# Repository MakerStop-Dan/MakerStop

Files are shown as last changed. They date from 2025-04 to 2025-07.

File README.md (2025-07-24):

# MakerStop
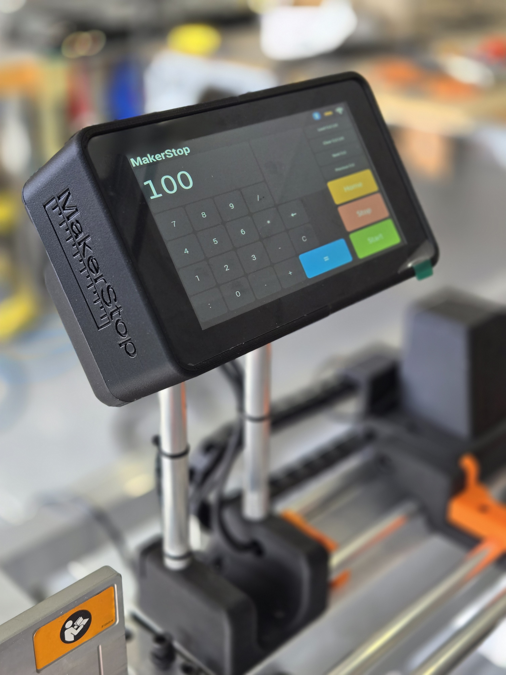
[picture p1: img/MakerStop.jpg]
MakerStop


Kits will be made available to purchase from www.makerstop.com.au

Contact - info@makerstop.com.au

Instagram - instagram.com/makerstop_

https://www.youtube.com/@MakerStop_au

**MakerStop** is an automatic length stop system designed for Mitre saws, band saws and drill presses used by Makers, metal fabricators, carpenters, and weekend warriors who demand precision without paying commercial-level prices.

Born out of necessity, MakerStop was developed in a small home garage where space, efficiency, and accuracy are the difference between thriving and burnout. As a full-time metal fabricator, I built this tool to meet the real-world demands of daily cutting tasks.

My goal is to make automation accessible—without the bloated cost or complexity. MakerStop is modular, lightweight, and affordable, and it challenges some of the typical assumptions in DIY automation and CNC hardware. If you're curious about how and why certain choices were made, check out the **Design Decisions** section below.

## Features
- Repeatable automatic stop positioning
- Mostly 3d Printed
- Easy assembly
- ESP32 Controller
- Raspberry pi zero 2w and custom python software for control
- Cut list functionality
- Customizable in length
- Low BOM cost
- Built for mitre saws, cold saws, drop saws, etc.

## 📄 License

- 🧠 **Software (code/scripts)** — [Mozilla Public License 2.0](https://www.mozilla.org/en-US/MPL/2.0/)
- 🛠️ **Design files (3D models, CAD, documentation)** — [CC BY-NC 4.0](https://creativecommons.org/licenses/by-nc/4.0/)

> Feel free to use, remix, and improve — just give credit.  
> Commercial use of hardware designs is **not allowed** without permission.  
> For licensing inquiries, reach out at info@makerstop.com.au

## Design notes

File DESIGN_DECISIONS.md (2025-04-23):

# MakerStop Design Decisions

The purpose of this page is to communicate my intentions through my design decisions. This includes the aspects of the project I consider most important, and the reasoning behind those priorities. It’s here to give context to current and future contributors, customers, or anyone digging into the project.

## Overview

MakerStop is a modular, 3D-printable automatic length stop system aimed at small fabrication shops, hobbyists, and maker spaces. It’s designed to be low-cost, highly customizable, and easy to assemble or maintain. The project balances printability, mechanical reliability, and accessibility.

**Key goals:**
- Must be adjustable in length to suit different applications
- Have an easy to use touch screen interface
- Cut list functionality 
- Needs to be light weight and compact enough to transport and ship
- Needs to be accurate and reliable

## Linear Motion

Linear motion is central to MakerStop’s function. Here's how I approached it:

- **Belt-Driven System:** I chose a GT3 timing belt as it is affordable, accurate and easy to source. A belt driven system allows for customizable length of motion. 
  
- **Linear Rails** The original prototype used linear rails and bearings as i had them left over from a CNC Build. While this is a great option, linear rails and bearings are expensive, heavy and difficult to source locally. 

I then worked on an MPCNC style carriage that used internally placed 15x5x5 Bearings. Another great option but it made for large complecated prints. 

I then took the Elon approach and began to question weather bearings were even necessary. In short, for this application, they aren't. I opted for 16mm round aluminium tube for the linear rails. The carriage hugs the rails with very little friction and allows for the affordability and modularity set out in the Goals section above. 

- **User Interface** It is tempting to build a mobile application to allow users to bring their own device but the decision was made to keep to the raspberry pi and touch screen interface to keep the user experience consistent and maintain a certain level of simplicity. 

**Firmware** FLUIDNC is a robust cnc firmware for ESP32 base controllers and works perfectly for this application. No need to reinvent the wheel. 

**Controller** Currently prototyping a custom controller design featuring ESP32 module and TB6600 stepper driver on the same board. It will also have a 5v rail to power the raspberry pi zero 2 and touch screen. Combining everything onto a single board will greatly reduce the space required in the touch screen enclosure, simplify the BOM and reduce the over all bom cost and assembly time.

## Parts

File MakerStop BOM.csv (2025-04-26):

 | QTY | Price | Total | Supplier
Raspberry Pi Zero | 1 | $29.45 | $506.12 | https://core-electronics.com.au/raspberry-pi-zero-2-w-wireless.html
Raspberry Pi SD Card 32gb | 1 | $17.20 |  | https://core-electronics.com.au/raspberry-pi-a2-class-sd-card-32gb.html
Raspberry Pi Touch Screen - WaveShare Disp -7a | 1 | $91.95 |  | https://core-electronics.com.au/7-touch-display-kit-for-raspberry-pi-zero-1024600-pixel-touch-screen.html
Limit Switch - Mechanical Key - Cherry MX | 1 | $2.45 |  | https://core-electronics.com.au/cherry-mx-switch.html
Nema 23 Stepper Motor high torque | 1 | $52.45 |  | https://www.makerstore.com.au/product/elec-nema23-635-ht
Stepper Driver - Pibot rev 2.3 | 1 | $22.00 |  | https://www.makerstore.com.au/product/pidrb230b01/
GT3 Timing Belt - 3m | 3 | $28.20 |  | https://www.makerstore.com.au/product/belt-gt3-1m/?pewc_key=503a48157eb3d2cdd4758ead74c50f1c
GT3 Pulley | 1 | $12.55 |  | https://www.makerstore.com.au/product/belt-gt3-10mm-635/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
Cable Chain 10x10 | 2 | $26.26 |  | https://www.makerstore.com.au/product/hard-dragchain-1010
Bearings 16x5x5 | 4 | $9.20 |  | https://www.makerstore.com.au/product/bear-6252rs/
Shielded Cable 6mm 4 core shielded | 4 | $17.64 |  | https://www.makerstore.com.au/product/elec-cable-4s-705
M5 x 10mm Cap Head Screws - Black - Pack of 10 | 1 | $1.26 |  | https://www.makerstore.com.au/product/bolt-m5-cap
M5 x 25mm Cap Head Screws - Black - Pack of 10 | 2 | $4.70 |  | https://www.makerstore.com.au/product/bolt-m5-cap
M8 x 20mm Cap Head Screws - Black - Pack of 10 | 1 | $4.20 |  | https://www.makerstore.com.au/product/bolts-m8-cap
Filament Pla CF 1kg - Black | 1 | $48.99 |  | https://au.store.bambulab.com/products/pla-cf
Filament PLA Matte - 1kg - Orange | 1 | $30.99 |  | https://au.store.bambulab.com/products/pla-matte?id=42647402381475
Power Supply 24v 7.5 amp adapter | 1 | $89.95 |  | https://www.auselectronicsdirect.com.au/24v-dc-7.5a-desktop-power-adapter-with-2.5mm-dc-pl
16mm Round Tube - Aluminium | 2 | $16.68

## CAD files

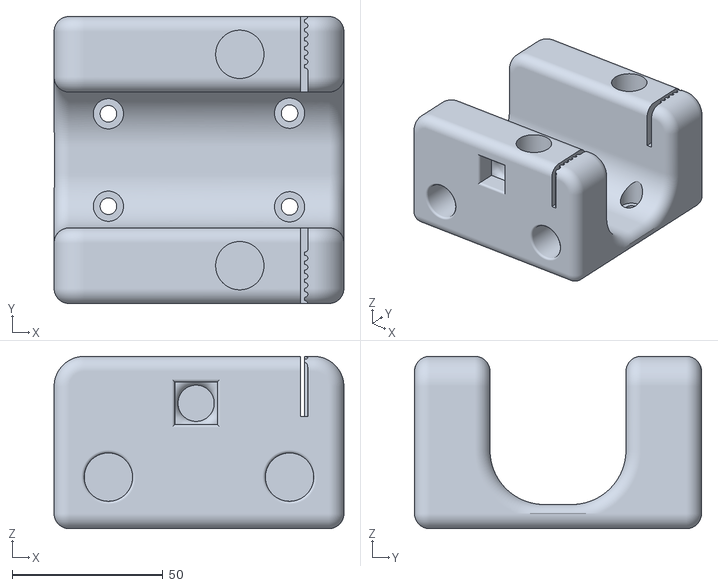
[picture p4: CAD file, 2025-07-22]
STL's/MakerStop - Home Base.stl
96.0 x 95.1 x 57.1

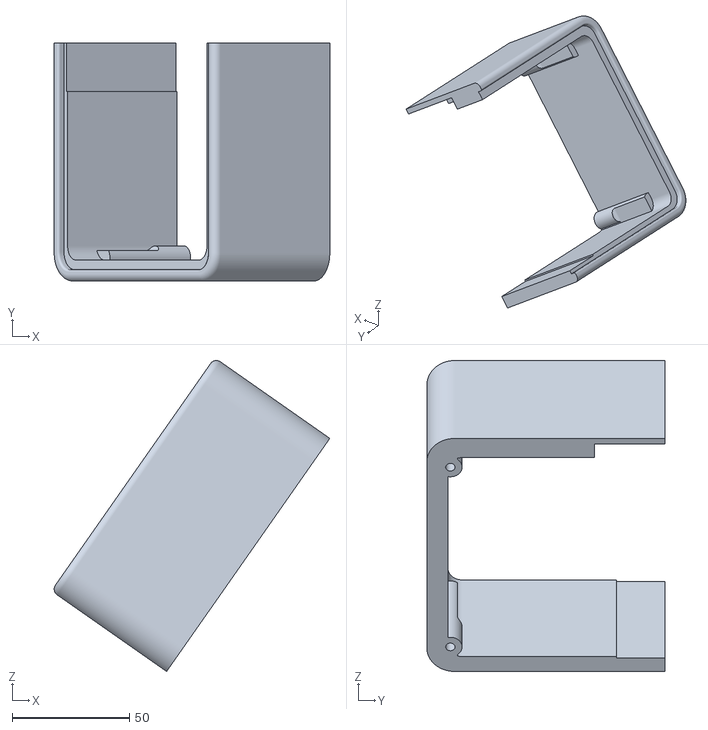
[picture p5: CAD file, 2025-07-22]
STL's/MakerStop - Console Right.stl
117.6 x 101.6 x 132.7

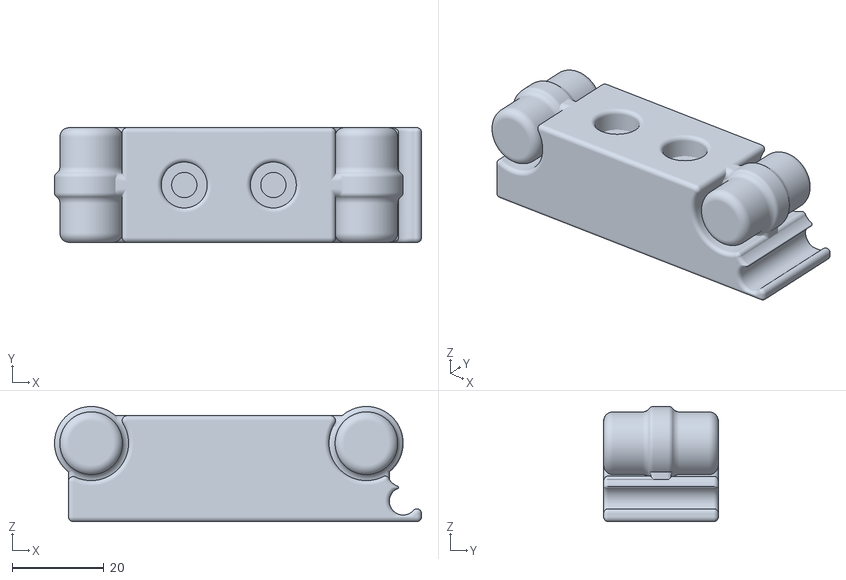
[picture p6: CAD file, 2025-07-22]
STL's/MakerStop - Rail Joiner .stl
80.0 x 25.0 x 25.1

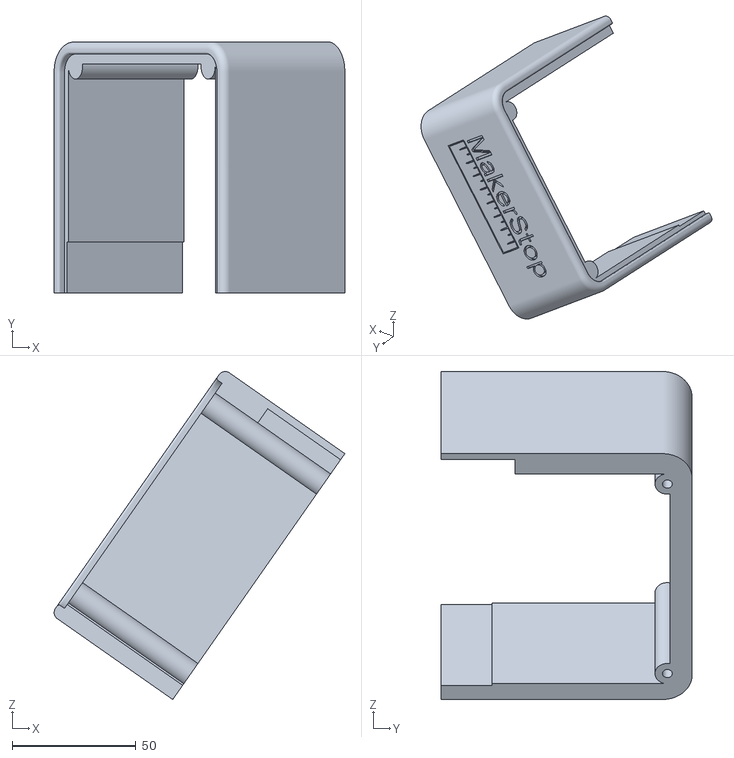
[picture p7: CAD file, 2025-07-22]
STL's/MakerStop - Console Left.stl
117.6 x 101.6 x 132.7

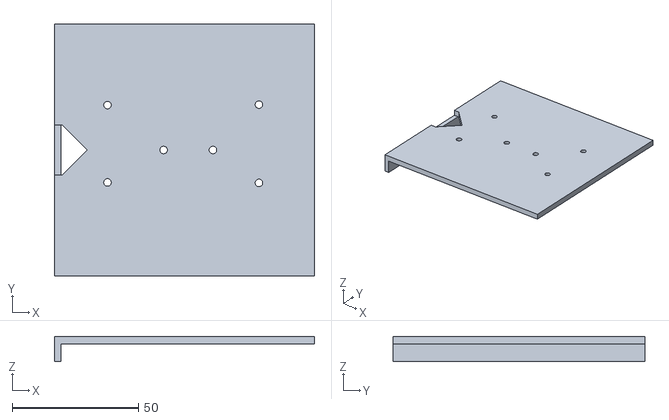
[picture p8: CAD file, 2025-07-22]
STL's/Marking jig.stl
103.0 x 100.0 x 10.0

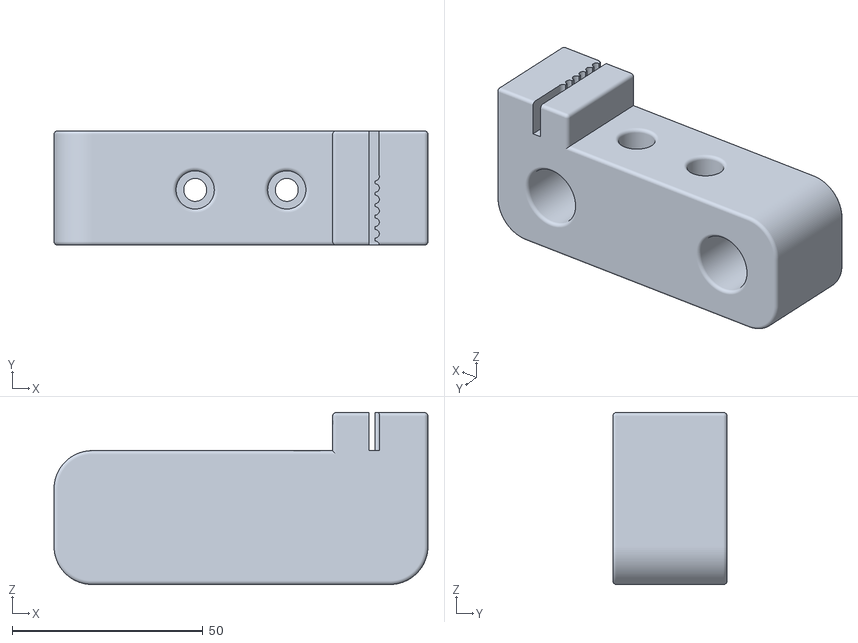
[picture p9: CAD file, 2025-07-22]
STL's/MakerStop - Rail End Mount.stl
98.0 x 30.0 x 45.1

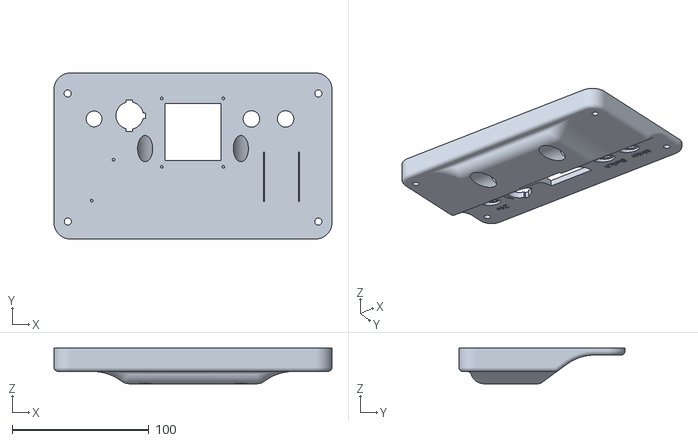
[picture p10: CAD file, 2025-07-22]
STL's/MakerStop - Console Back .stl
203.2 x 121.4 x 26.0

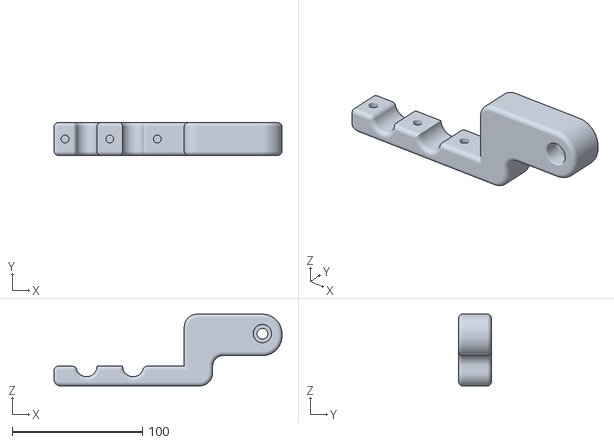
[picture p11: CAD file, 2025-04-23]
STL's/MakerStop - Carriage Arm Bottom Right.stl
175.0 x 25.0 x 55.1

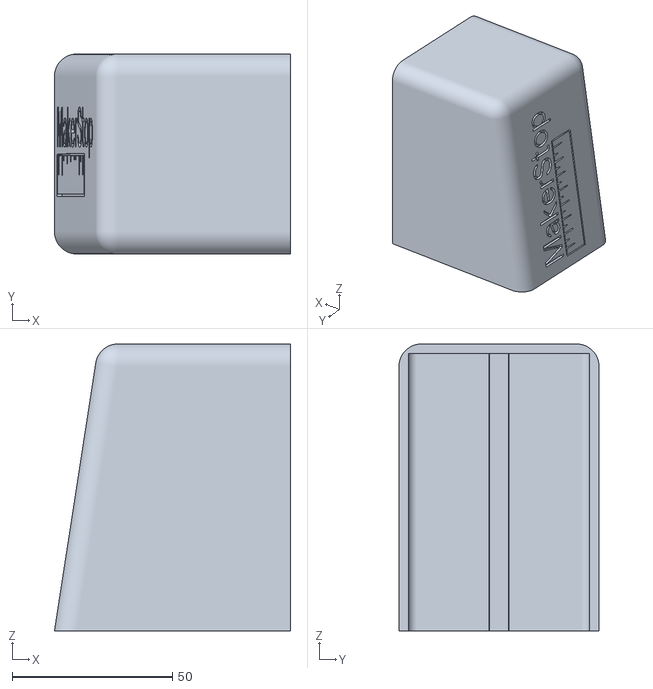
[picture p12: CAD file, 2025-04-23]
STL's/MakerStop - Motor Cover.stl
73.6 x 62.4 x 89.5

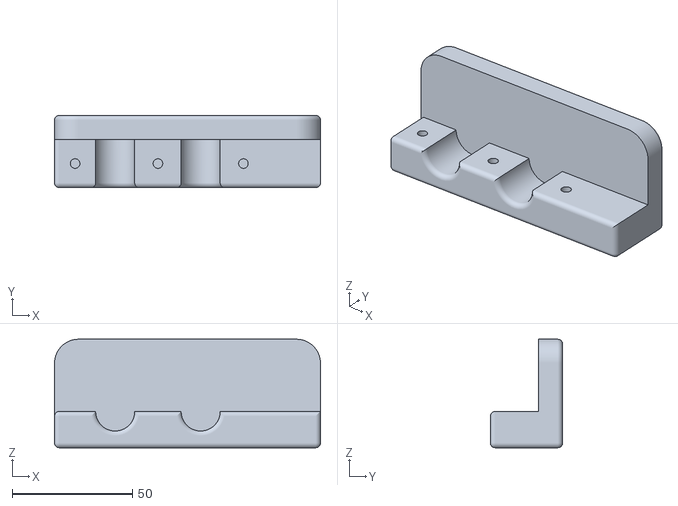
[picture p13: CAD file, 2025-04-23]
STL's/MakerStop - Stop Block.stl
110.5 x 30.0 x 45.1

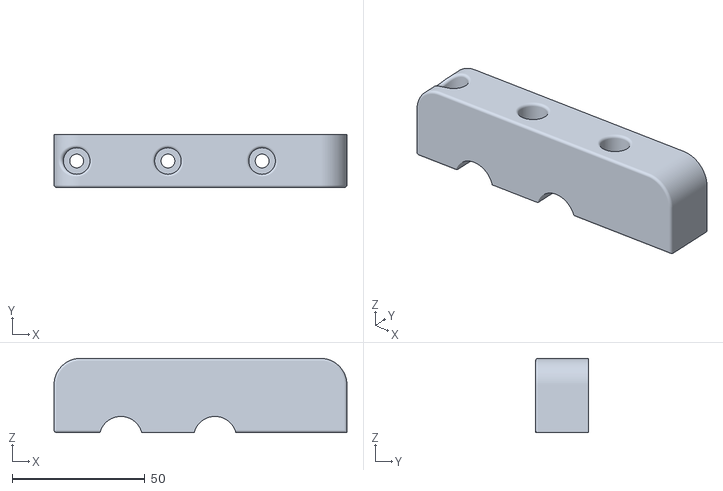
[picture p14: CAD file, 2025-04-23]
STL's/MakerStop - Stop Clamp.stl
110.5 x 20.0 x 28.0

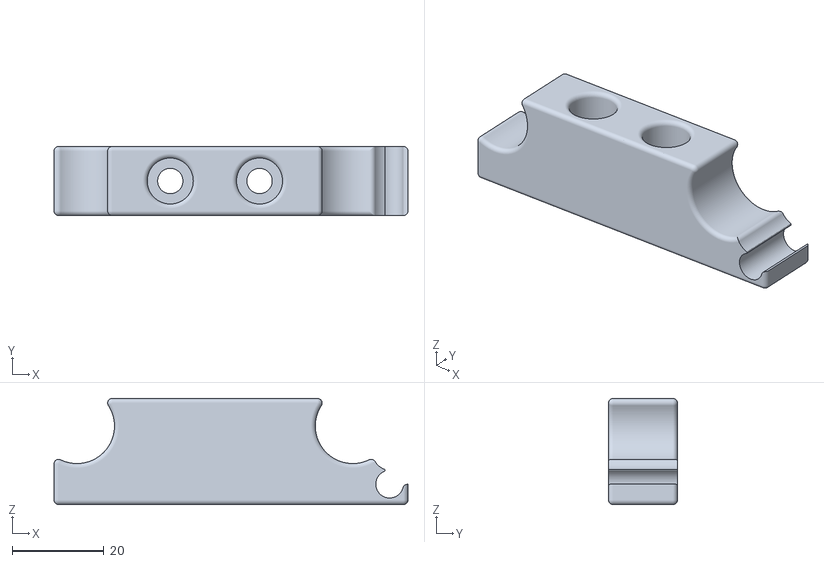
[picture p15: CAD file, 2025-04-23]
STL's/MakerStop - Rail Support.stl
77.0 x 15.0 x 23.1

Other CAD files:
STL's/MakerStop - Carriage Arm Bottom Left.stl

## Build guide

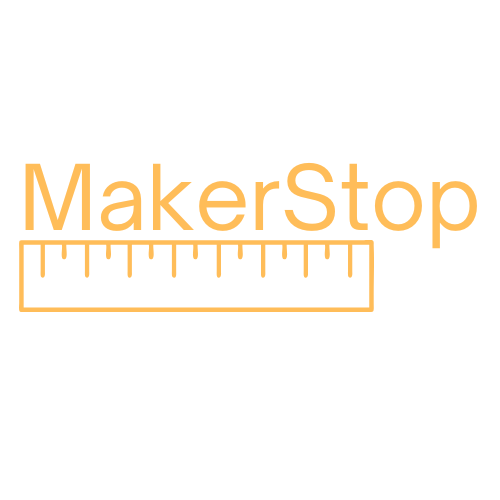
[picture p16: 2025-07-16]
Code/assets/MakerStop.png

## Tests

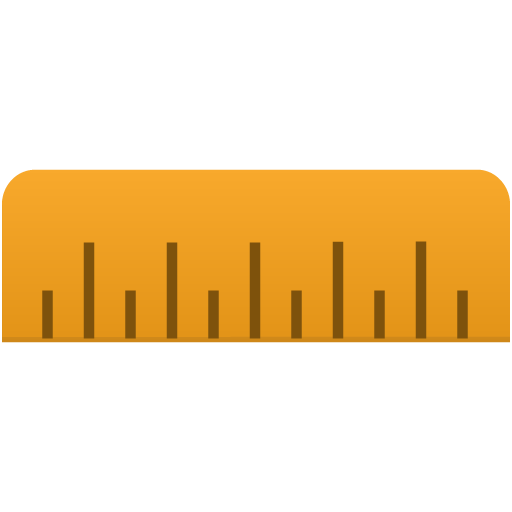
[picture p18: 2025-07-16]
Code/assets/calibrate.png

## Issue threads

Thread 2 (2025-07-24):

PCB Design

MakerStop-Dan, 2025-07-24:
I'd like to design a custom pcb for the makerstop which combines all of the current hardware into a single board. The main componants/features are:

1) esp32 devkit or module
2) TB6600 stepper driver
3) 5v output to power the raspberry pi zero 2 W
4) 24v input
5) Trim pot for setting driver current
6) Dip switches to control micro stepping
7) Testing points for measuring current to stepper driver.

The PCB should have mounting holes to suit the female posts on the back of the raspberry pi zero touch screen (see BOM for model) to allow for easy assembly.

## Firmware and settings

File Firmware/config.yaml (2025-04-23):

board: ESP32 wroom Dev Kit
name: MakerStop
stepping:
  engine: RMT
  idle_ms: 255
  pulse_us: 4
  dir_delay_us: 0
  disable_delay_us: 0
  segments: 12
kinematics: {}
axes:
  shared_stepper_disable_pin: NO_PIN
  shared_stepper_reset_pin: NO_PIN
  
  
  x:
    steps_per_mm: 13.307
    max_rate_mm_per_min: 15000
    acceleration_mm_per_sec2: 500
    max_travel_mm: 2400
    soft_limits: false
    motor0:
      limit_neg_pin: gpio.18:low:pu
      limit_pos_pin: NO_PIN
      limit_all_pin: NO_PIN
      hard_limits: false
      pulloff_mm: 3
      standard_stepper:
        step_pin: gpio.32
        direction_pin: gpio.14
        disable_pin: NO_PIN

    homing:
      cycle: 2
      allow_single_axis: true
      positive_direction: false
      mpos_mm: 0
      seek_mm_per_min: 5000
      feed_mm_per_min: 200
      seek_scaler: 1.5
      feed_scaler: 1.5
coolant:
  flood_pin: NO_PIN
  mist_pin: NO_PIN
  delay_ms: 0
macros: {}
start:
  must_home: false
  deactivate_parking: false
  check_limits: true
parking:
  enable: false
  axis: Z
  target_mpos_mm: -5
  rate_mm_per_min: 800
  pullout_distance_mm: 5
  pullout_rate_mm_per_min: 250
user_outputs:
  analog0_pin: NO_PIN
  analog1_pin: NO_PIN
  analog2_pin: NO_PIN
  analog3_pin: NO_PIN
  analog0_hz: 5000
  analog1_hz: 5000
  analog2_hz: 5000
  analog3_hz: 5000
  digital0_pin: NO_PIN
  digital1_pin: NO_PIN
  digital2_pin: NO_PIN
  digital3_pin: NO_PIN
  digital4_pin: NO_PIN
  digital5_pin: NO_PIN
  digital6_pin: NO_PIN
  digital7_pin: NO_PIN
user_inputs:
  analog0_pin: NO_PIN
  analog1_pin: NO_PIN
  analog2_pin: NO_PIN
  analog3_pin: NO_PIN
  digital0_pin: NO_PIN
  digital1_pin: NO_PIN
  digital2_pin: NO_PIN
  digital3_pin: NO_PIN
  digital4_pin: NO_PIN
  digital5_pin: NO_PIN
  digital6_pin: NO_PIN
  digital7_pin: NO_PIN
arc_tolerance_mm: 0.002
junction_deviation_mm: 0.01
verbose_errors: true
report_inches: false
enable_parking_override_control: false
use_line_numbers: false
planner_blocks: 16

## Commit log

2025-04-23 STL Upload
    [MakerStop - Carriage Arm Bottom Left.stl, MakerStop - Carriage Arm Bottom Right.stl, MakerStop - Console Back.stl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]
2025-04-26 Upload BOM
    [MakerStop 1.0 BOM.csv]
2025-04-26 Update MakerStop - Console Back.stl
    [MakerStop - Console Back.stl]
2025-07-16 BOM Rename
    [MakerStop BOM.csv]
2025-07-17 Cut List Server
    Added Cutlist server and web interface. Access in browser using makerstop:5000
2025-07-22 STL Update
    [MakerStop - Console Left.stl, MakerStop - Console Back .stl, MakerStop - Console Back.stl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]
2025-07-22 Updated Cut List Manager
    Can now edit cut lists in browser.
2025-07-31 Update calibration.py
    Instead of selecting a measurement to test, there is now an input field.
